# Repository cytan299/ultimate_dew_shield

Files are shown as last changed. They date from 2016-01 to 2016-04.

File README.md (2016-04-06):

# The Ultimate Dew Shield

by C.Y. Tan 2016

Ultimate Dew Shield

I looked at the commercially available dew shields for my 8" LX200 and
I thought that I could do better. The requirements for my dew shield
are as follows:

* I want my dew shield to be perfectly fitted on my LX200 that takes
  into account the optical rails that are mounted on both the top and
  bottom of my LX200.
* I want a temperature controller for the dew shield that
measures both the dew point as well as the ambient temperature. The
controller will use these temperature measurements to set the
internal temperature of the dew shield to a differential temperature
that is set by the user.

## Support

All the software have been successfully compiled on Mac OS X 10.10.5
(Yosemite) and 10.11.2 (El Capitan) running Arduino IDE 1.6.5. Note:
Later versions of Arduino IDE cannot compile the Arduino Pro Micro
library. See the README.md in the arduino directory for more
information.

This is unsupported software and hardware. Build at your own peril! :)

You can submit questions or bug reports using the
[issues](https://github.com/cytan299/ultimate_dew_shield/issues) tab on
the right and then click on **NEW**.

Have fun!

## Directory structure

* **arduino** The C++ code for the Arduino Pro Micro.
* **arduino_case** The case design for the controller.
* **bom** Bill of materials for 1 ultimate dew shield. 
* **eagle** Eagle schematic and board files.
* **howto** Guides for how to assemble the dew shield and the
controller.
* **controller_analysis** The analysis of the temperature control
loop.
* **writeup** A writeup of the motivation and analysis of the
  Ultimate Dew Shield.

## Other information

More information can be found in he *README.md* files in each
directory and the [wiki](https://github.com/cytan299/ultimate_dew_shield/wiki/The-Ultimate-Dew-Shield) of this project on github.

## Copyright
All the software, documentation, hardware that I have written is
copyright 2016 C.Y. Tan.

All software is released under GPLv3

All documentation is released under Creative Commons
Attribution-ShareAlike 3.0 Unported License or GNU Free
Documentation License, Version 1.3

All hardware is released under CERN Hardware Open License v1.2

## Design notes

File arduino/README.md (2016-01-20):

# Arduino source code

This directory contains the arduino source code for the Arduino Pro
Micro. The code has been successfully compiled using ARDUINO 1.6.5. It
**cannot** be compiled with later versions of the ARDUINO IDE because
the Pro Micro library is unsupported (as of 01 Jan 2016)! Sparkfun
knows about this and will eventually release a library that is
compatible with later versions of the ARDUINO IDE. Please follow the
instructions
[here](https://learn.sparkfun.com/tutorials/pro-micro--fio-v3-hookup-guide)
for installing the Pro Micro libraries.

## Note

The code assumes that _Tinside_ has index 0 and _Toutside_ has
index 1. You can change these indices by changing the defines TIN and
TOUT in the _controller.ino_ file.

## Directories

* **controller** This contains the *controller.ino* file which is the entry point
for the controller program.
* **lib** This contains the libraries which are required for compiling
  *controller*. The README.md file contains more information about
  these libraries.

## Copyright

The software that is written by the author is copyright 2016 C.Y. Tan
and released under GPLv3.

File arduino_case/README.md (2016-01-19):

# Arduino case

This is the case that I designed for the controller. 

The file *ponoko_submitted_v2.svg* file can be uploaded to [Ponoko](http://www.ponoko.com) for manufacture. The material that I used is

* Acrylic - Clear - Abrasion Resistant
* 3.0 mm thick
* P1 - 181.0 mm long x 181.0 mm wide

## Copyright

The case design is copyright 2016 C.Y. Tan and released under the CERN Open Hardware License v1.2

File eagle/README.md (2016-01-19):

# Eagle files

These are the eagle files that can be sent to pc board manufacturers to
be made. There is a free version of [eagle](http://cadsoftusa.com)
that can be downloaded to view the designs.

## Directories

* **controller** The controller module is mounted on the dew
  shield. It monitors the temperatures inside and outside the dew
  shield, and the relative humidity.

## Copyright

The schematic and board designs are copyright 2016 C.Y. Tan and
released under the CERN Open Hardware License v1.2

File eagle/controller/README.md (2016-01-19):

# Controller Module

The controller module is mounted on the dew shield. It monitors the
temperatures inside and outside the dew shield, and the relative
humidity.

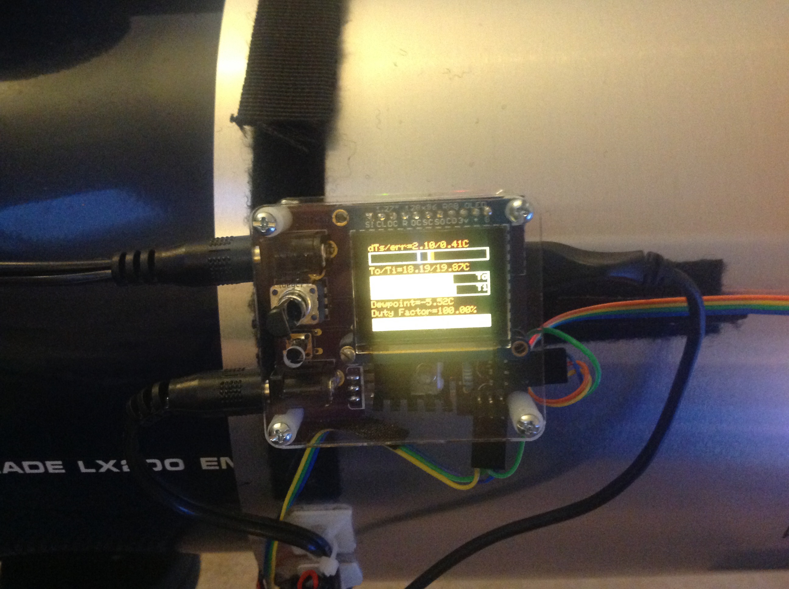
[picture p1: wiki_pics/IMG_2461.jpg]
Controller Module


## Copyright

The schematic and board designs are copyright 2016 C.Y. Tan and
released under the CERN Open Hardware License v1.2

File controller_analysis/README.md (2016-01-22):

# Analysis of the control loop

I measured the step response of the control loop when it and my dew
shield  is installed on my LX200. I used the step response to
simulate the performances of a P and PI control loops. And from these
simulations, I found that a P loop is good enough for keeping the
differential temperature between the outside and inside of the dew
shield to better than 0.5 degC.

## Copyright

This article is copyright 2016 C.Y. Tan and released under Creative Commons
Attribution-ShareAlike 3.0 Unported License.

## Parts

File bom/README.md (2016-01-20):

# Bill of Materials

I present the estimated cost for building *one* Ultimate Dew Shield
here to be about $280. This is the lower bound for the cost of one
such device because, in practise, it is not possible to just buy 1
screw :) or is it cost effective to buy just one pcb, and the required
tools, like a soldering iron, are already on hand. Plus, I did not
include tax or cost of shipping. I would imagine that if people banded
together to build multiple copies of this device, the cost will get
closer to $280.

The bom.ods file is readable using [LibreOffice Calc](http://www.libreoffice.org).

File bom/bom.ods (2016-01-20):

Part # | Description | Price each | # required | Cost of 1 | Bought from | Total cost of 1 | Shield only
COM-09288 | Rotary pot 10 kohms | $0.95 | 1 | $0.95 | www.sparkfun.com | $229.69 | $39.49
COM-10213 | N-channel mosfet 60V 30A | $0.95 | 1 | $0.95 | www.sparkfun.com
COM-11289 | Heating pad 5*15 cm | $4.95 | 4 | $19.80 | www.sparkfun.com
DEV-12640 | Arduino Pro Micro | $19.95 | 1 | $19.95 | www.sparkfun.com
PRT-00117 | Breakaway headers – Machine pin | $2.95 | 1 | $2.95 | www.sparkfun.com
PRT-00743 | Breakaway female headers | $3.95 | 1 | $3.95 | www.sparkfun.com
PRT-10687 | High temperature adhesive tape | $4.95 | 0.1 | $0.50 | www.sparkfun.com
PRT-11417 | Stackable headers | $1.50 | 0.25 | $0.38 | www.sparkfun.com
SEN-00245 | 1 -wire digital temperature sensor | $4.25 | 3 | $12.75 | www.sparkfun.com
SEN-08733 | Jumper wire 3 pin | $1.50 | 1 | $1.50 | www.sparkfun.com
109322 | fuse holder, 22AWG*3” | $0.79 | 1 | $0.79 | www.jameco.com
2258355 | 5V@3A, power supply | $9.95 | 1 | $9.95 | www.jameco.com
69439 | fuse, 3A fast acting | $0.35 | 1 | $0.35 | www.jameco.com
2188625 | power jack, 2.1 mm | $0.35 | 1 | $0.35 | www.jameco.com
2099121 | DC extension cable | $2.95 | 1 | $2.95 | www.jameco.com
1115643 | Heat sink TO-220 | $0.35 | 1 | $0.35 | www.jameco.com
34121 | Heat sink mounting kit | $0.20 | 1 | $0.20 | www.jameco.com
1673 | Oled 1.27” | $34.95 | 1 | $34.95 | www.adafruit.com
49821683146 | 14*10 aluminum flashing | $10.24 | 1 | $10.24 | home depot
77579023335 | duct insulation | $18.77 | 1 | $18.77 | home depot
75967900861 | 3/4”*5 ft velcro (cost is per foot) | $1.49 | 2 | $2.99 | home depot
7098182806 | Black caulk (dynaflex) | $4.48 | 1 | $1.49 | home depot
 | Black felt | $1.99 | 3 | $5.97 | hobby lobby
67668 | Rivets (500 count) | $0.01 | 2 | $0.02 | Harbor Freight Tools
CAB-10646 | 15 ft 6 wire ribbon cable | $2.95 | 0.2 | $0.59 | www.sparkfun.com
COM-12792 | Right angle 2*40 breakaway headers | $1.95 | 0.3 | $0.59
PRT-10452 | Screw 1/2” 4-40 | $0.15 | 0 | $0.00
PRT-10453 | Screw 1/4” 4-40 | $0.15 | 0 | $0.00
PRT-10927 | 3/8” nylon standoff | $0.30 | 0 | $0.00
PRT-11796 | 3/4” nylon standoff | $0.40 | 0 | $0.00
SEN-09569 | HIH-4030 humidity sensor | $16.95 | 1 | $16.95
1025816 | Plast-I-Weld | $4.49 | 1 | $4.49 | www.hobby.com (http://www.hobbylobby.com/)
1025824 | Fine tip line applicator | $4.99 | 1 | $4.99
153106 | Spanish Copper Rub'n Buff | $5.99 | 1 | $5.99
 | PCBs | $7.67 | 1 | $7.67 | oshpark.com
887480029819 | 4-40 1.25” screws and nuts | $0.30 | 0 | $0.00
30699370917 | 4-40 1.5” screws and nuts | $0.30 | 4 | $1.18 | www.homedepot.com
887480149180 | nylon spacer 1/2” | $0.28 | 8 | $2.20
 | nylon spacer 1/4” | $0.45 | 2 | $0.90
 | laser cut box | $13.60 | 1 | $13.60 | www.ponoko.com
167249 | Thermal compound | $8.95 | 1 | $8.95 | www.jameco.com
2045350 | 0.1” low profile pins | $3.99 | 1 | $3.99 | www.jameco.com
157383 | 3 pin housing | $0.29 | 2 | $0.58 | www.jameco.com
A3001 | 26-22 contact pins for 3 pin housing | $0.66 | 6 | $3.95 | www.digikey.com
1981 | 4 mm nylon spacer | $0.04 | 1 | $0.04 | www.pololu.com

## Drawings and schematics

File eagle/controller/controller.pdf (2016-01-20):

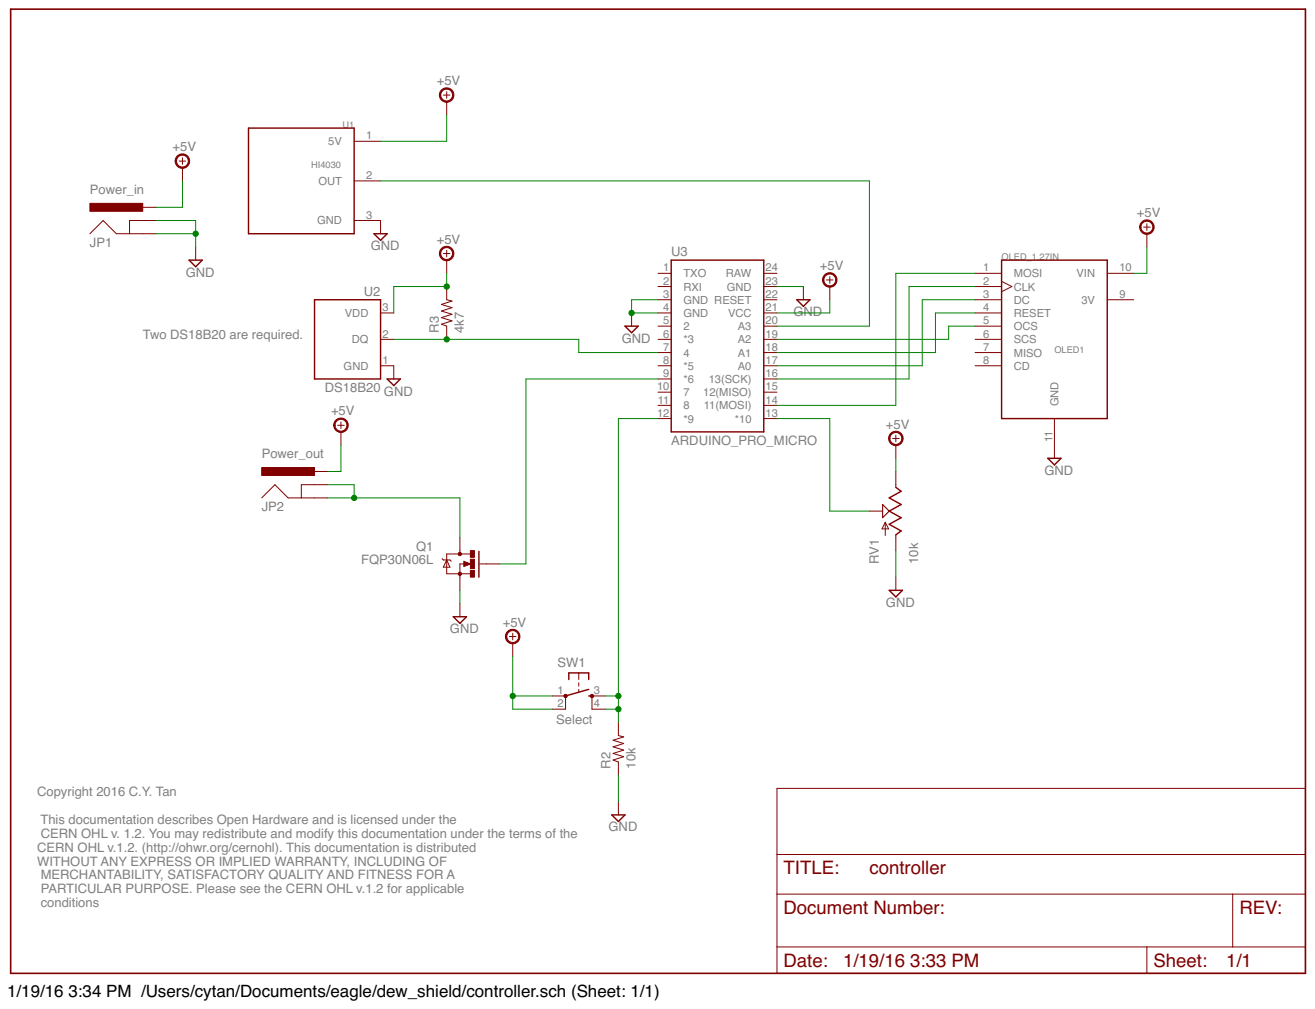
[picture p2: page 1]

Copyright 2016 C.Y. Tan This documentation describes Open Hardware and is licensed under the CERN OHL v. 1.2. You may redistribute and modify this documentation under the terms of the CERN OHL v.1.2. (http://ohwr.org/cernohl). This documentation is distributed

WITHOUT ANY EXPRESS OR IMPLIED WARRANTY, INCLUDING OF
MERCHANTABILITY, SATISFACTORY QUALITY AND FITNESS FOR A
PARTICULAR PURPOSE. Please see the CERN OHL v.1.2 for applicable
conditions

Document Number: | REV:

Date: 1/19/16 3:33 PM | Sheet: 1/1

1/19/16 3:34 PM /Users/cytan/Documents/eagle/dew_shield/controller.sch (Sheet: 1/1)

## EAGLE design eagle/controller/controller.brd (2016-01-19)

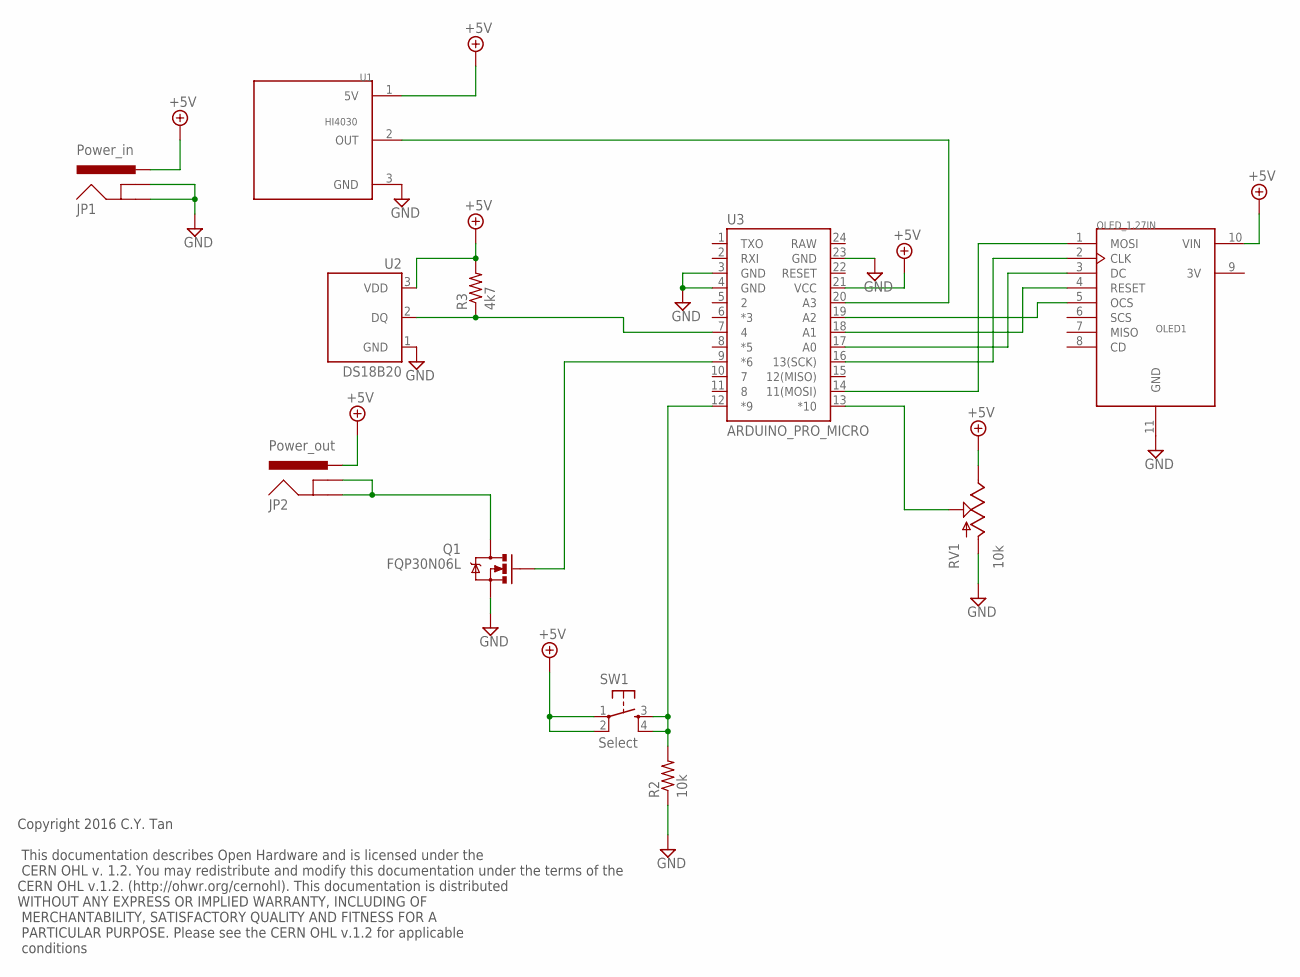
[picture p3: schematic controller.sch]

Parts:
JP1: Power_in; POWER_JACK_PTH
JP2: Power_out; POWER_JACK_PTH
OLED1: OLED_1.27IN; OLED_1.27INCH
Q1: FQP30N06L; TO220V
R2: 10k; AXIAL-0.3
R3: 4k7; AXIAL-0.3
RV1: 10k; ALPS_POT_KIT
SW1: Select; TAC-SWITCH-PTH
U1: HI4030; 1X03
U2: DS18B20; TO-92-AMMO
U3: ARDUINO_PRO_MICRO

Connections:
3V: OLED1.9 (3V)
+5V: JP1.PWR, JP2.PWR, OLED1.10 (VIN), R3.P$2 (2), RV1.P$1 (E), SW1.1, SW1.2, U1.1 (5V), U2.3 (VDD), U3.21 (VCC)
GND: JP1.GND, JP1.GNDBREAK, OLED1.11 (GND), Q1.3 (S), R2.P$1 (1), RV1.P$3 (A), U1.3 (GND), U2.1 (GND), U3.3 (GND), U3.4 (GND), U3.23 (GND)
unnamed: OLED1.1 (MOSI), U3.14 (11(MOSI))
unnamed: OLED1.2 (CLK), U3.16 (13(SCK))
unnamed: OLED1.3 (DC), U3.17 (A0)
unnamed: JP2.GND, JP2.GNDBREAK, Q1.2 (D)
unnamed: OLED1.4 (RESET), U3.18 (A1)
unnamed: OLED1.5 (OCS), U3.19 (A2)
unnamed: Q1.1 (G), U3.9 (*6)
unnamed: RV1.P$2 (S), U3.13 (*10)
unnamed: R2.P$2 (2), SW1.3, SW1.4, U3.12 (*9)
unnamed: U1.2 (OUT), U3.20 (A3)
unnamed: R3.P$1 (1), U2.2 (DQ), U3.7 (4)

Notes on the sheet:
Copyright 2016 C.Y. Tan This documentation describes Open Hardware and is licensed under the CERN OHL v. 1.2. You may redistribute and modify this documentation under the terms of the CERN OHL v.1.2. (http://ohwr.org/cernohl). This documentation is distributed WITHOUT ANY EXPRESS OR IMPLIED WARRANT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

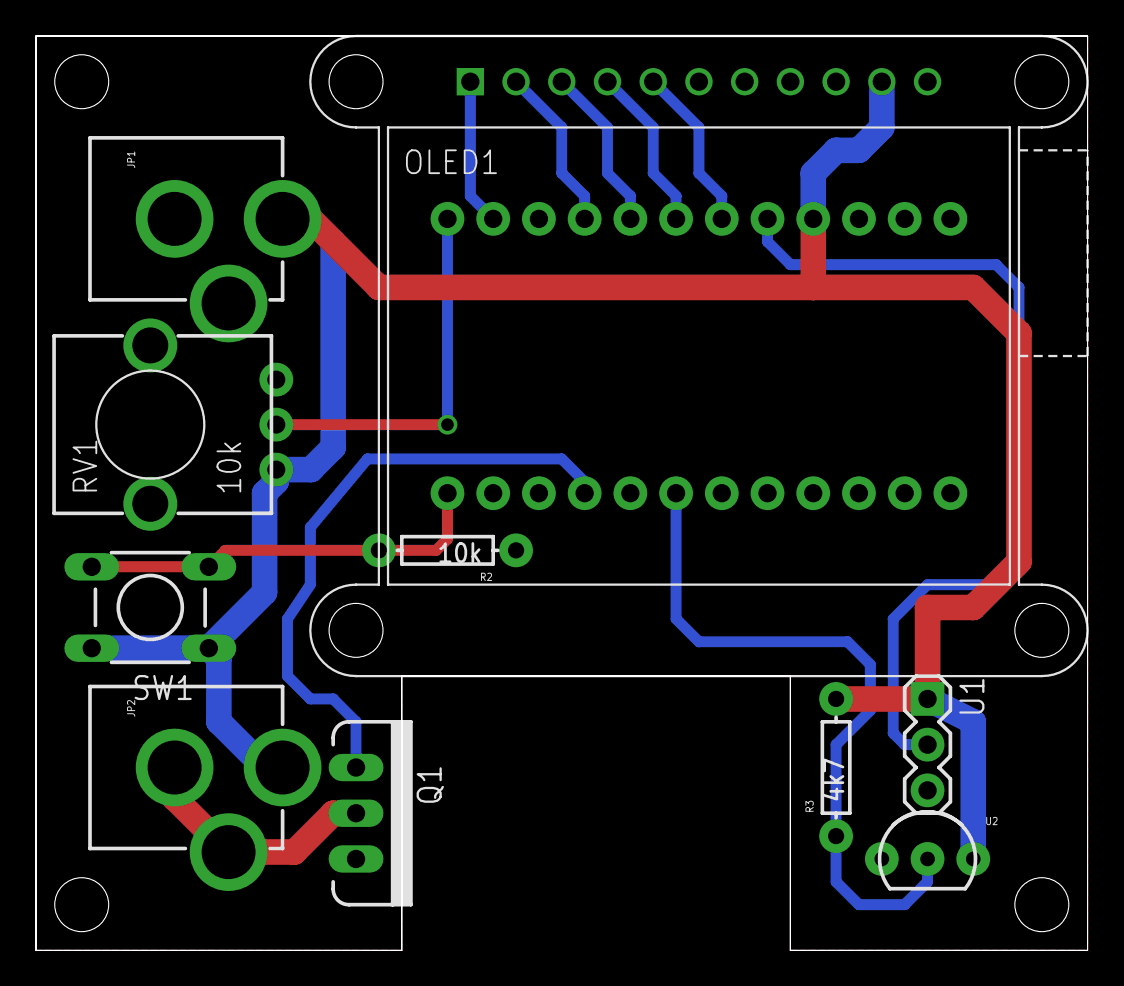
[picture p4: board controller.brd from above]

Board: 2 copper layers, 58.4 x 50.8 mm, 11 parts (1 on the bottom side), 13 nets.

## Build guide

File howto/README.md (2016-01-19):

# How to build the Ultimate Dew Shield

I have written these two documents to help you build and assemble my
Ultimate Dew Shield.

## The documents

* **dew_shield.pdf** This guide tells you how I assembled the
  parts of thedew shield. 
* **controller.pdf** This guide tells you how I assembled the 
controller. It only points out the important parts in the construction
because I have assumed that you know how to solder electronic
componics to the pcb.

## Copyright

These documents are copyright 2016 C.Y. Tan and released under
Creative Commons Attribution-ShareAlike 3.0 Unported License.

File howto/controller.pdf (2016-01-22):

## Temperature controller assembly instructions

C.Y. Tan
1/21/16

## Chip board roll

2 | Controller Assembly | January 21, 2016

## License

Copyright 2016 C.Y. Tan
This document is licensed under Creative Commons Attribution-ShareAlike 3.0 Unported License. To view a copy of this license, visit http://creativecommons.org/licenses/by-sa/3.0/

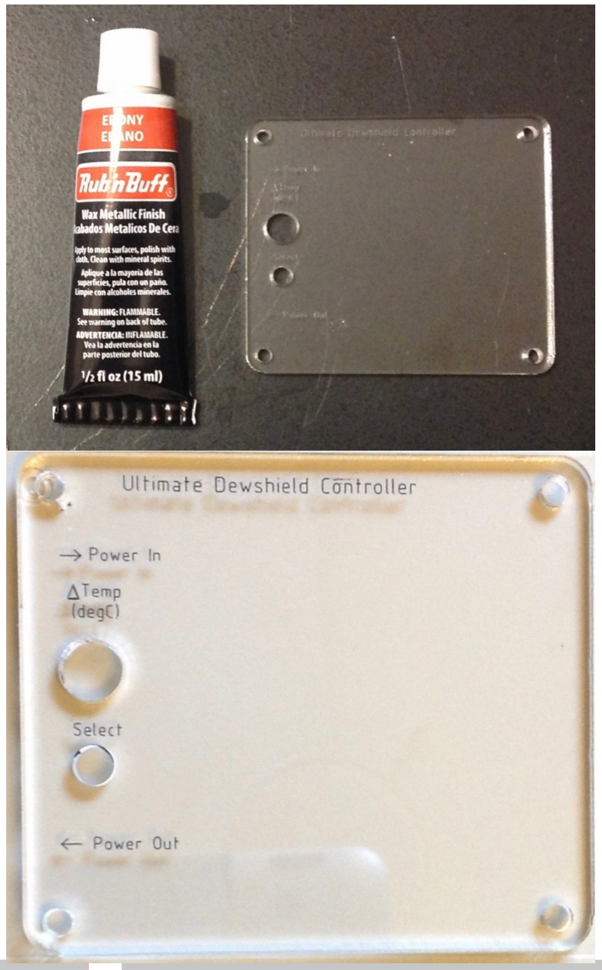
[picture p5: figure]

3 | Controller Assembly | January 21, 2016

## Preparing the top cover

The lettering on the top cover can only be seen after it has been filled in with some Rub N'Buff.

Use a little rubbing alcohol to clean off the access after rubbing in Rub N'Buff.

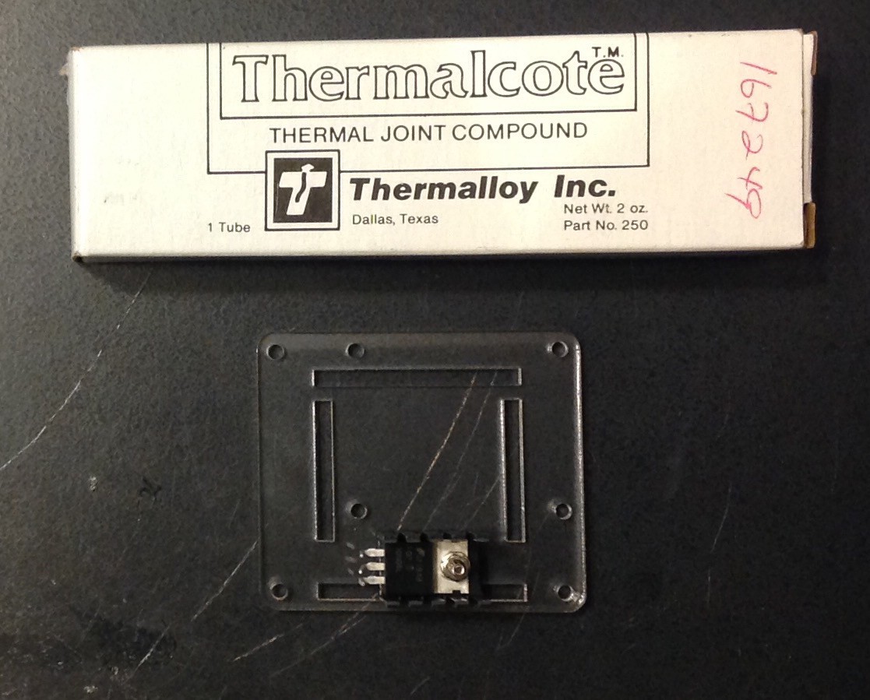
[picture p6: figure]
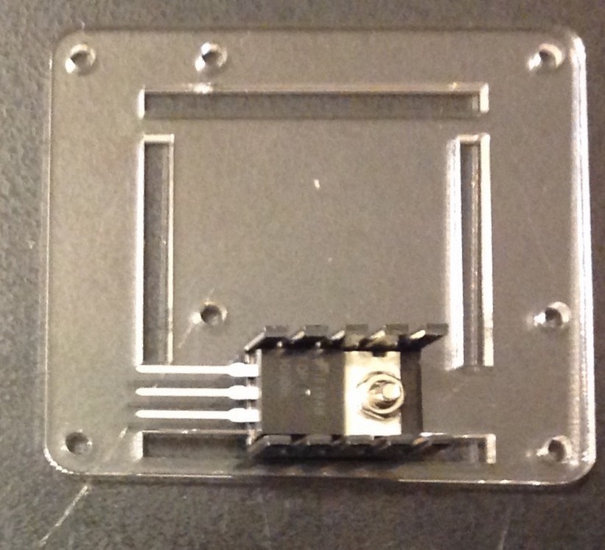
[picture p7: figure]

4 | Controller Assembly | January 21, 2016

## Installing the MOSFET and heatsink to the back cover

The MOSFET must be screwed onto the heat sink with a thin layer of thermal compound and then mounted onto the back cover. Make sure that the orientation of the cover is correct!

Bend and adjust the legs of the MOSFET so that it will go through its mounting holes on the PCB when the PCB is mounted on its 1/2” spacers.

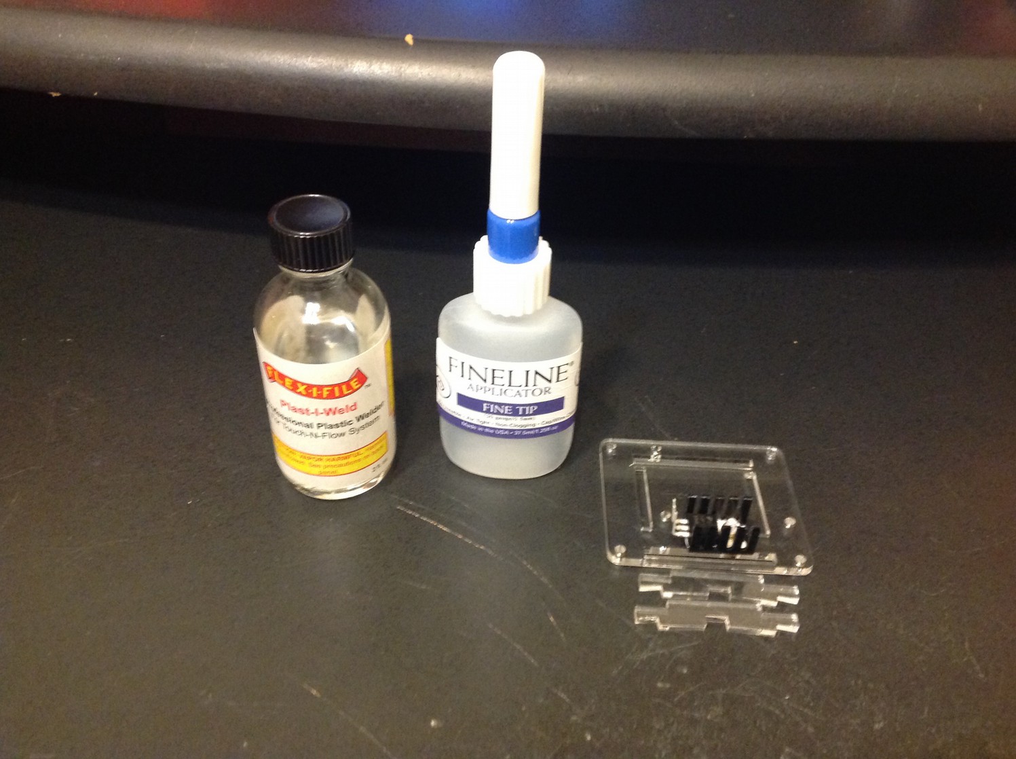
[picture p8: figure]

5 | Controller Assembly | January 21, 2016

## Cementing the supports onto the back cover

You will have to first select the direction that you want to attach temperature controller to the dew shield.

I wanted to attach the controller to the side of the dew shield and so I'm using the shorter curve supports.

Use an acrylic cement with a fine line applicator to weld the acrylic supports together. A youtube video from this link (https://www.youtube.com/watch?v=hT6Ow_cBTps) shows you how. If there is any overflow or drops of cement that land on the acrylic, do not wipe it off! Let it dry by itself and there will not be a trace of it dries.

I did not add the cross beams until I installed the PCB because I wanted to be able to further adjust the MOSFET during the PCB installation. Once the cross beams are installed, the head of the MOSFET's screw is basically inaccessible.

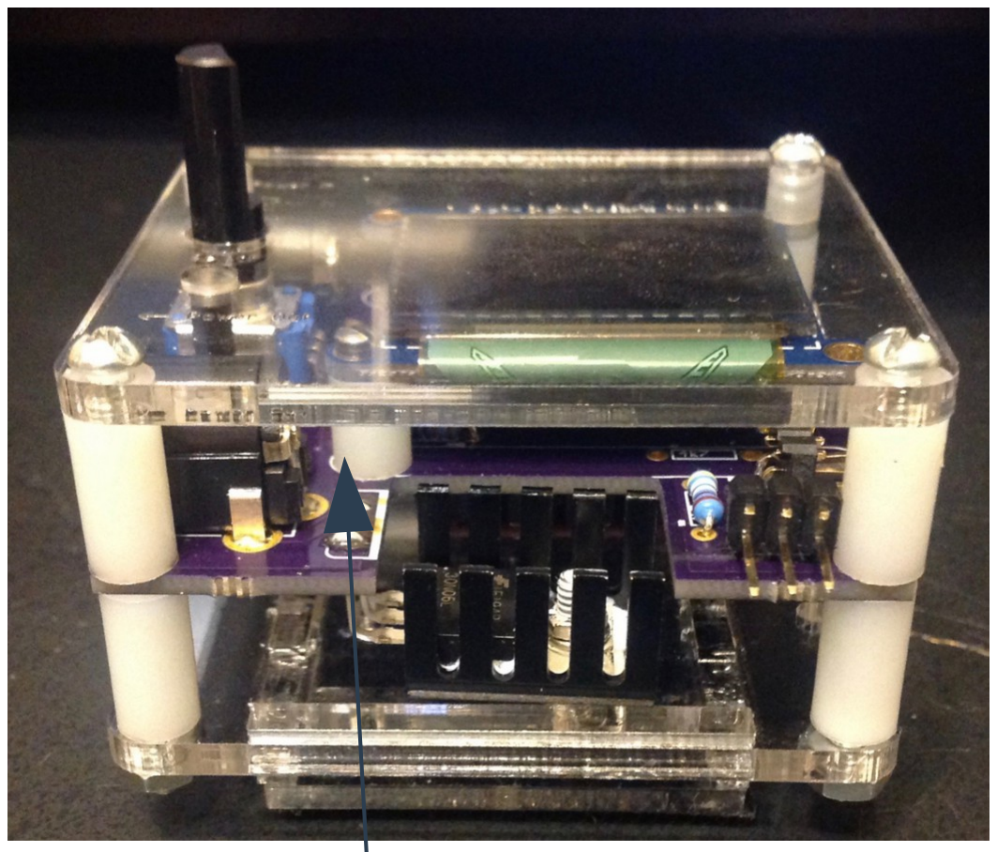
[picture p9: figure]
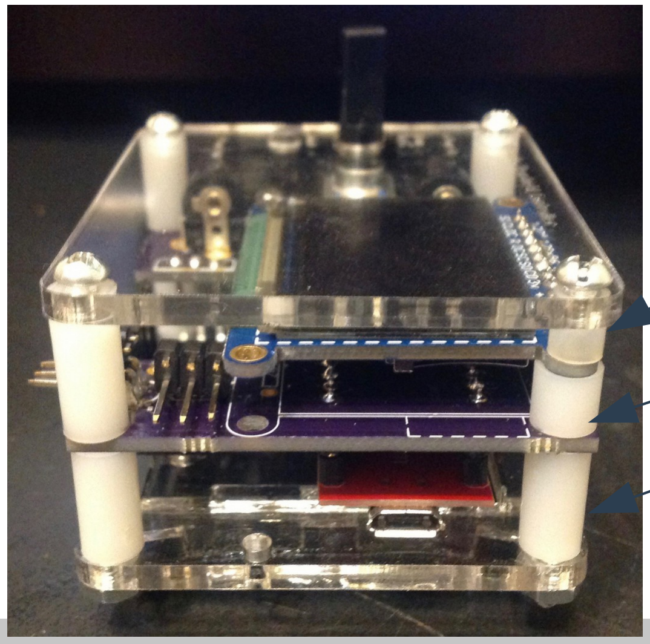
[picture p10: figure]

6 | Controller Assembly | January 21, 2016

## Assembling the top and bottom covers to the PCB

The covers and PCB are attached with 1.5” 4-40 screws and ½ inch nylon standoffs.

The OLED is securely attached to the PCB using two 1/4” nylon standoffs. The OLED and the top cove with s a 4 mm spacer. In order to get this spacing, you must use the low profile 0.1” spacing pins from www.jameco.com, (http://www.jameco.com/webapp/wcs/stores/servlet/ProductDisplay?search_type=jamecoall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) and the sockets from www.sparkfun.com. (https://www.sparkfun.com/products/743)

4 mm

1/4”

1/2”

1/4”

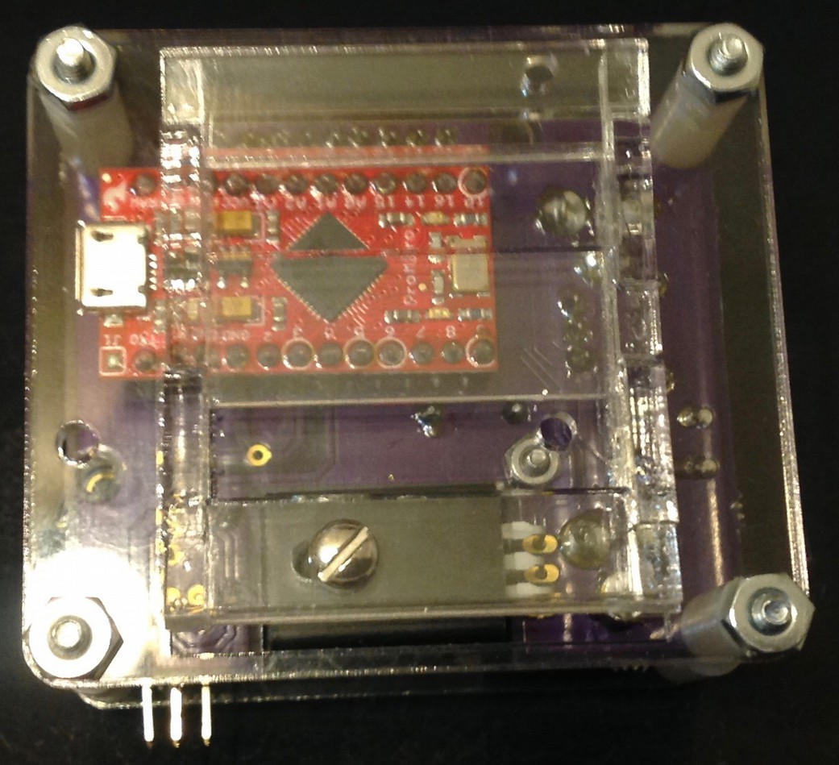
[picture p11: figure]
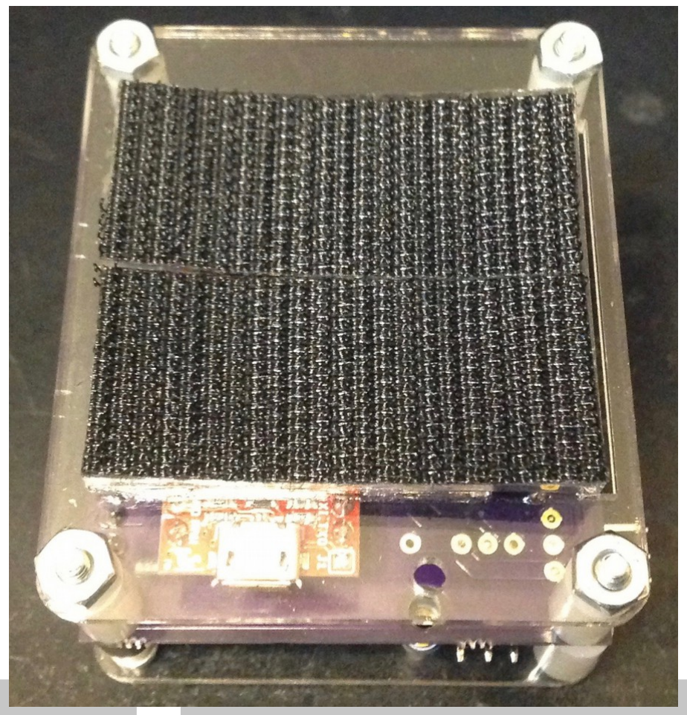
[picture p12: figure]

7 | Controller Assembly | January 21, 2016

## Add cross beam supports and velcro

Next, the cross beam supports are cemented.
The MOSFET can be soldered to the PCB after all its components are soldered on.
The top and bottom covers are attached with 1.5” screws with 1/2” spacers.

Velcro is stuck to the curved support structure.

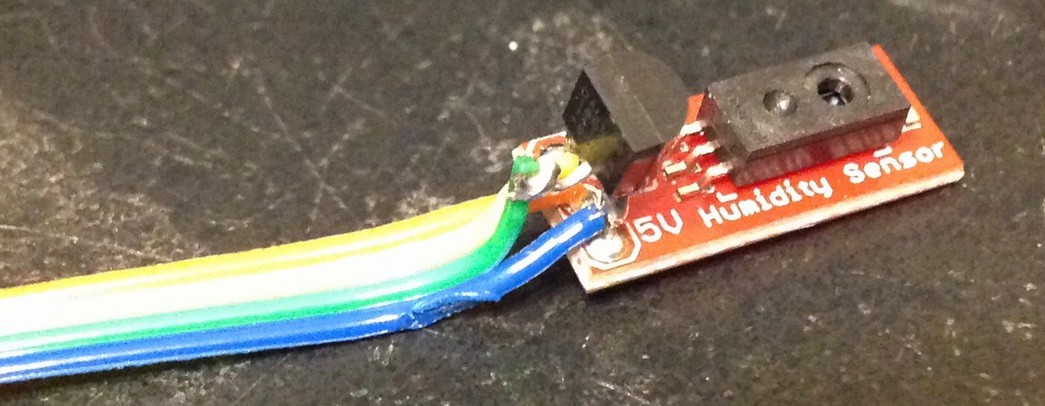
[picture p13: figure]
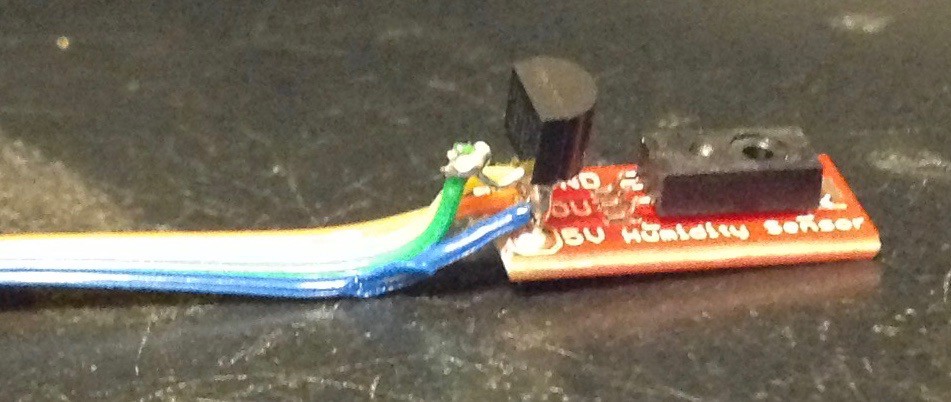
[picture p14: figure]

8 | Controller Assembly | January 21, 2016

## Adding DS18S20 to the humidity sensor

The temperature probe DS18S20 is soldered to the humidity sensor with its middle pin raised.

A 4 wire ribbon cable is used to connect the DS18S20/humidity sensor to the controller. Make sure the ribbon cable is long enough to reach where you want to mount the controller on the dew shield.

The GND and Power wires are soldered to the DS18S20 because they are common to both the DS18S20 and the humidity sensor.

The middle leg of the DS18S20 is raised and a wire is soldered to it. The last wire is soldered directly to the middle hole of the humidity sensor.

Make sure that you have the wires correctly matched at the other end for power/ground, DS18S20 out and humidity sensor out. The colored wires help tremendously here!

## Making the sensor harness

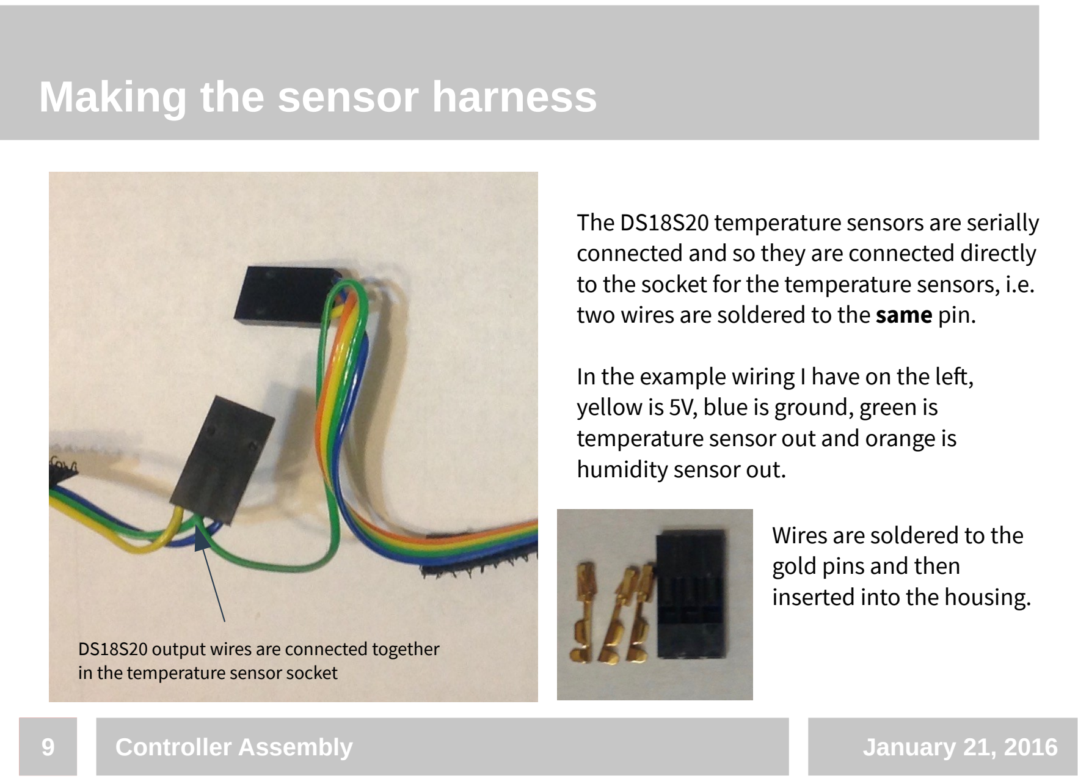
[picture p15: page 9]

9 | Controller Assembly | January 21, 2016

The DS18S20 temperature sensors are serially connected and so they are connected directly to the socket for the temperature sensors, i.e. two wires are soldered to the same pin.

In the example wiring I have on the left, yellow is 5V, blue is ground, green is temperature sensor out and orange is humidity sensor out.

DS18S20 output wires are connected together in the temperature sensor socket

Wires are soldered to the
gold pins and then
inserted into the housing.

## Making the temperature probe mounted inside the dew shield

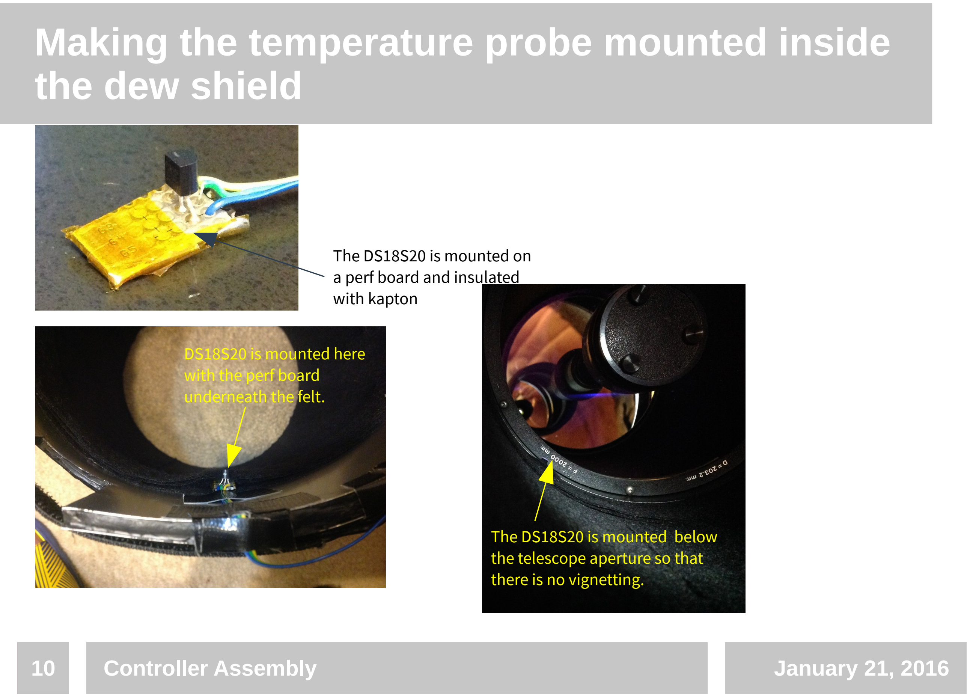
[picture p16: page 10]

10 | Controller Assembly | January 21, 2016

The DS18S20 is mounted on
a perf board and insulated with kapton

DS18S20 is mounted here
with the perf board
underneath the felt.

The DS18S20 is mounted below the telescope aperture so that there is no vignetting.

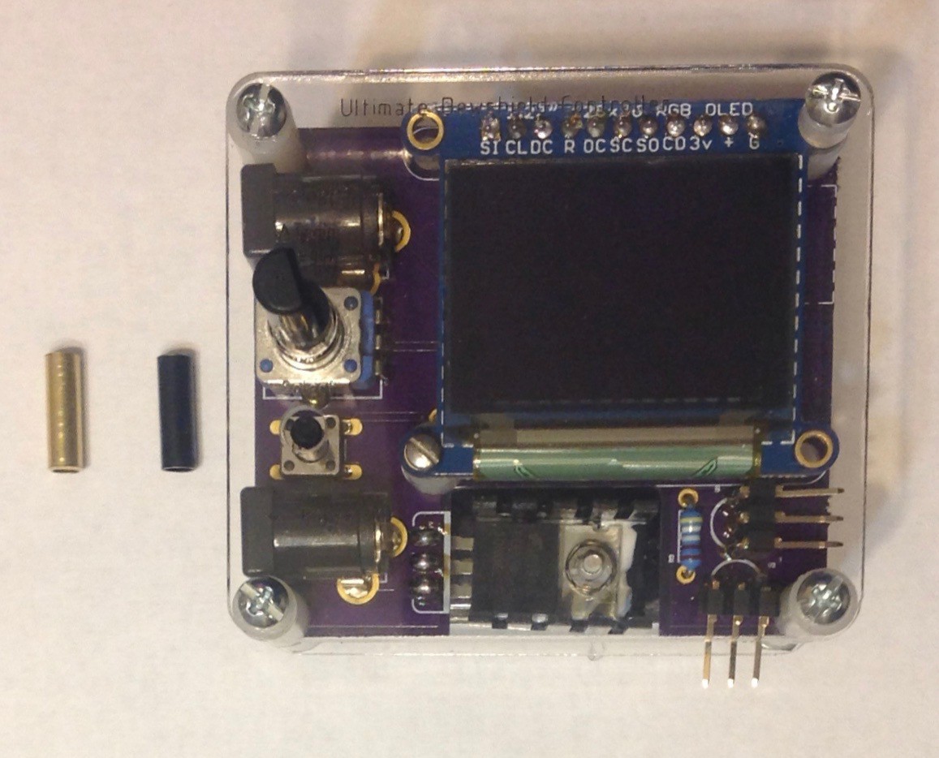
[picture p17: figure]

11 | Controller Assembly | January 21, 2016

## Making the push button (optional)

The push button switch is recessed below the front cover. In order to reach the button, I made a push button with a brass tube OD=5/32” and length 1/2” to reach it. I painted it black to keep the color scheme consistent.

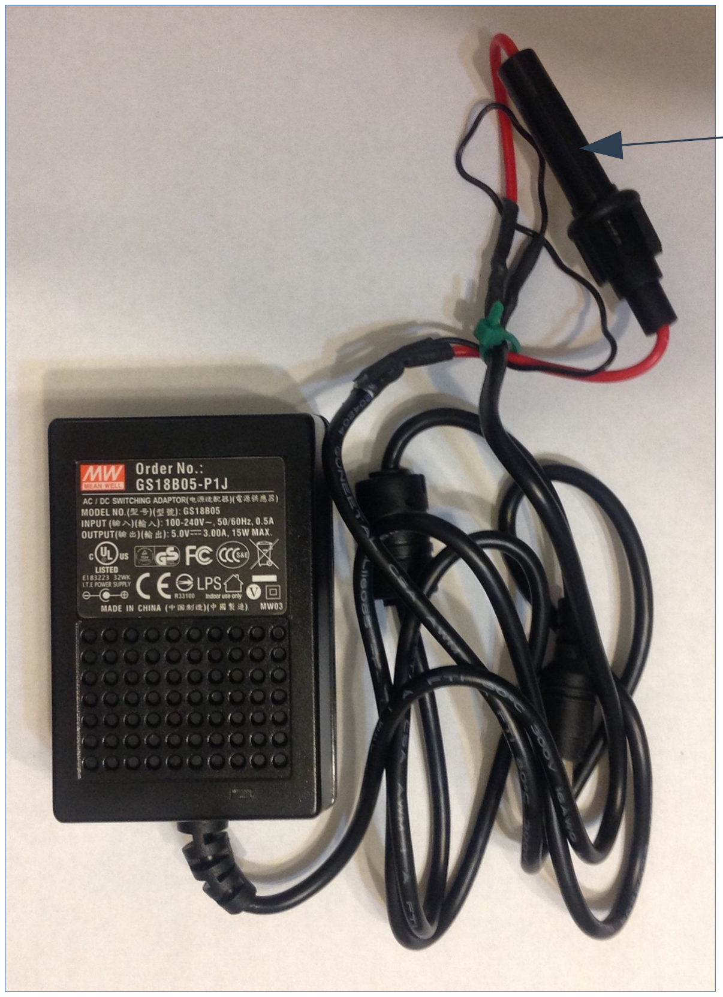
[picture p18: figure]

12 | Controller Assembly | January 21, 2016

## Adding a fuse to the power supply

Fuse holder with 3A
fast acting fuse

I added a 3 A fuse to the output of the 5V, 3A power supply as a safety precaution. In principle, the current should never exceed 2.5 A.

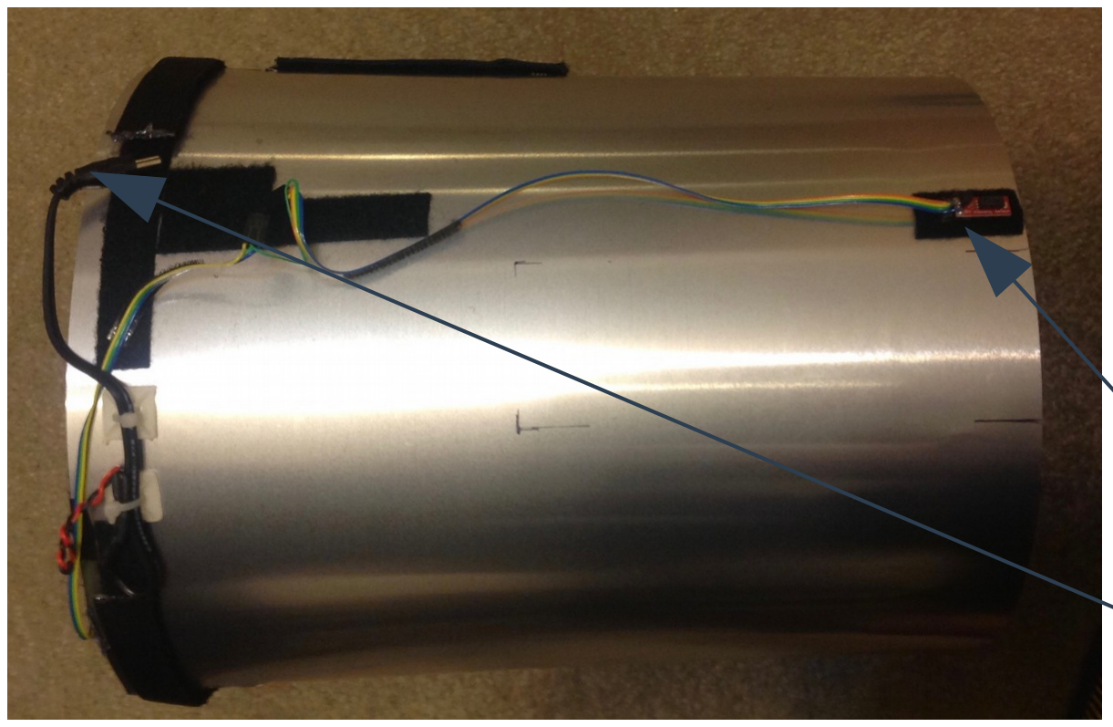
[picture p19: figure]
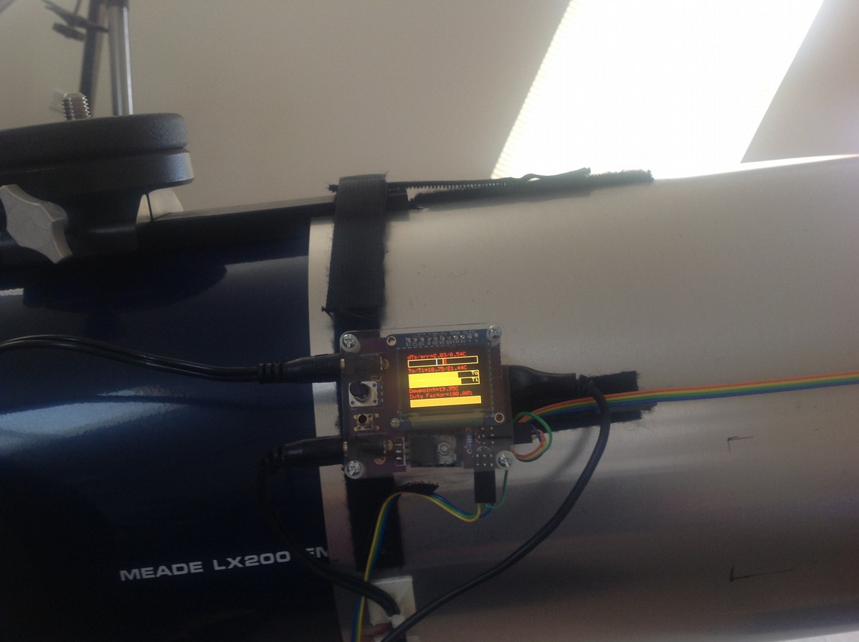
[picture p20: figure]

13 | Controller Assembly | January 21, 2016

## Mounting the controller

Finally, the controller is mounted onto the dew shield with the power, heat pad cable, and the sensor cables connected. Once powered up, it keeps the inside of the dew shield at a set temperature above the ambient or the dew point at a level determined by the user using the pot.

Velcro pads are stuck on the locations where the humidity sensor and the controller will be set.

Humidity sensor
Connector to heating pads

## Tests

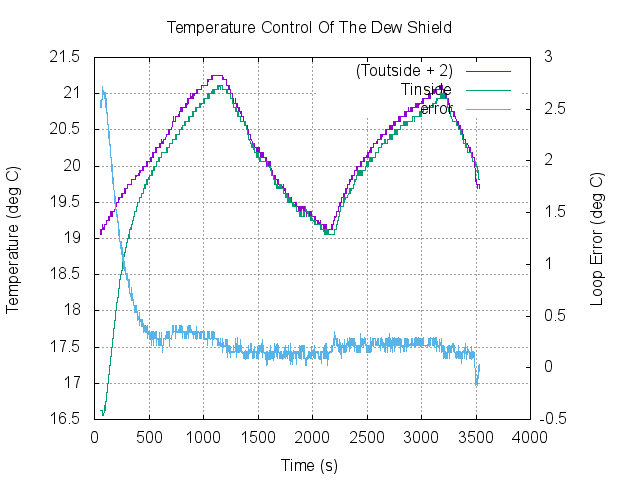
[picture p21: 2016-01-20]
wiki_pics/track_results1.png

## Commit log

2016-01-19 Initial commit. Still missing are: (a) in howto subdirectory: controller.pdf (b) writeup on how the controller works.
    [bom.ods, controller.brd, controller.sch]
2016-01-20 bom: Updated bill of materials. eagle: Updated controller.sch and controller.pdf. howto: Added controller.pdf.
    [bom.ods, controller.sch]
2016-01-20 arduino: Updated controller code to send measurement data out whenever a USB cable is connected
2016-01-20 arduino: Updated README.md and controller.ino
2016-01-21 howto: Added slide about fuse in controller.pdf
2016-01-22 arduino: Push button now toggles between full info and min info displays.
2016-01-22 howto: controller.pdf: removed statement that push button is not used.
2016-01-25 arduino: Updated synopsis

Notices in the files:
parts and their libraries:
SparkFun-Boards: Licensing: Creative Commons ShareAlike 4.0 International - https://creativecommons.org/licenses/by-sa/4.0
